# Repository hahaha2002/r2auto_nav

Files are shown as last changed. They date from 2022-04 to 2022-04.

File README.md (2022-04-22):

# r2auto_nav
Tánkyu 2310i <br/>
Group 2, Studio 2 <br/>
Ang Kai Jun, David Chong Joon Wei, Ha Zhe Li, Rayner Lim Fang Yuh, Wang Yanxiao Austin <br/>

EG2310 - Fundamentals of Systems Design, AY 21/22, <br/>
Innoovation and Design Programme, National University of Singapore (NUS). <br/>
Screen_Shot_2022-04-22_at_00 24 10_AM-removebg-preview

## Description
The Tánkyu 2310i, developed by NUS IDP students from EG2310, is a modified Robotis Co. Turtlebot 3. It is augmented with LIDAR, NFC-detection, IR-detection and a flywheel firing system to accomplish its set objectives - Autonomous navigation within a closed and connected maze, locating a loading bay demarcated by NFC tags, and firing a ping-pong ball at a target with high IR-signature.

In this repository, we are using Ubuntu 20.04.4, ROS2 Foxy and Python3.6 to explore a closed and connected maze using a left-wall following algorithm.
You may check out our project report under the [Documentations](https://github.com/hahaha2002/r2auto_nav/tree/main/Documentations) folder for more details on our robot and its mission.

## File Organisation
- [Documentations](https://github.com/hahaha2002/r2auto_nav/tree/main/Documentations) folder contain all the documentation of the Tánkyu 2310i, this includes the project report, assembly manual, full software setup guide and end user documentation.
- [navigation.py](https://github.com/hahaha2002/r2auto_nav/blob/main/navigation.py) code contains the main system and wall-following logic. This code also communicates with the mission code to allow the Tánkyu 2310i to engage on the ir signature when the conditions are met.
- [mission.py](https://github.com/hahaha2002/r2auto_nav/blob/main/mission.py) code initiates all the i2c connections and contain the firing algorithm. This code performs all necessary logic processing with the input from the NFC and IR detection systems and communicates the information to the navigation code to allow the Tánkyu 2310i to engage on the ir signature when the conditions are met.
- [Ubuntu_Files](https://github.com/hahaha2002/r2auto_nav/tree/main/Ubuntu_Files) folder is an archive of the miscellaneous code that was tested but not implemented into the final system. The code are functional independently but requires some edits to integrate it into the final system.
- [RPi_Files](https://github.com/hahaha2002/r2auto_nav/tree/main/RPi_Files) folder contains the [factory acceptance test codes](https://github.com/hahaha2002/r2auto_nav/tree/main/RPi_Files/fac_test), all required packages and other test codes for each individual subsystem. 
- [Original_Files](https://github.com/hahaha2002/r2auto_nav/tree/main/Original_Files) folder is an archive of the forked repository from [shihchengyen's r2auto_nav_repository](https://github.com/shihchengyen/r2auto_nav) and is not necessary for the Tankyu 2310i's operations.

## Calibration and configuration
### Navigation Code
Under 'Adjustable variables to calibrate wall follower', you may experiment with different parameters to calibrate the navigation algorithm to suit your needs.
| Variable name| Description| Recommended value  |
| --- |:---| ---:|
| d | Distance from wall| 0.35 |
| fd| Front distance when approaching a merging wall| d + 0.1|
| reverse_d | Distance to reverse when too close to front wall| 0.20|
| speedchange | Linear speed | 0.17|
| turning_speed_wf_fast| Fast rotate speed, used when avoiding obstacle in front| 0.75|
| turning_speed_wf_slow| Slow rotate speed, used when reversing, finding wall or too close to wall| 0.40|
| snaking_radius | Distance from wall before correcting drift | d - 0.07|
| cornering_speed_constant | Coefficient of speedchange during cornering to prevent over/under steer| 0.5|

### Mission Code
Under 'Adjustable variables to calibrate targeting' you may experiment with different parameters to calibrate the targeting algorithm to suit your needs.
| Variable name| Description| Recommended value  |
| --- |:---| ---:|
| rotatechange | Angular speed| 0.35 |
| speedchange | Linear speed | 0.20 |
| min_temp_threshold | IR live feed minimum value reference (Appears blue) | 30.0|
| max_temp_threshold | IR live feed maximum value reference (Appears red) | 35.0|
| detecting_threshold | Minimum temperature to identify target as a "Hot target" | 32.0|
| firing_threshold | Acts as a second check after centering target | 35.0|
| ir_offset | Offset angle for each IR sensor orientation (0°→0, 45°→31, 90°→69) | 31.0|

## Operating Instructions

### Installation
Tested on Ubuntu 20.04 - ROS2 Foxy <br/>
For beginners, follow our step-by-step software setup guide in our [documentations](https://github.com/hahaha2002/r2auto_nav/tree/main/Documentations) folder.<br/>
For M1 MacBook users, refer to our [video guide](https://youtu.be/suntoEurFio) for Ubuntu setup and installation. <br/>

1. Install Ubuntu 20.04 and ROS 2 Foxy using the instructions in Section 3.1 of the [Robotis e-manual](https://emanual.robotis.com/docs/en/platform/turtlebot3/quick-start/#pc-setup) (Ensure you click on the "Foxy" tab).
3. Using Ubuntu, complete the RPi in Section 3.2
4. Using Ubuntu, complete the OpenCR setup in Section 3.3 

### Set Up
1. Clone this repository onto your Ubuntu ros2 directory: <br/>
``` 
cd colcon_ws/src/auto_nav
git clone https://github.com/hahaha2002/r2auto_nav.git 
cd colcon_ws
colcon build
```
2. Copy mission.py and the RPi_files folder to the RPi: <br/>
``` 
scp -r <path to r2auto_nav directory>/mission.py ubuntu@<RPi IP address>:~/turtlebot_ws/src 
scp -r <path to r2auto_nav directory>/RPi_files ubuntu@<RPi IP address>:~/turtlebot_ws/src 
```
3. Build the package on RPi: <br/>
``` 
cd turtlebot3_ws 
colcon build 
```
4. Install the pigpio package on RPi and automate the daemon on boot:
```
sudo apt install pigpio
sudo systemctl enable pigpiod
```

### Running Instructions
1. Ssh into the RPi, `ssh ubuntu@<RPi IP Address>`
2. On the RPi, initiate the bring up `ros2 launch turtlebot3_bringup robot.launch.py'
3. On RPi, in the RPi_files directory, Start the targeting code `python3 mission.py`.
4. On Ubuntu, in the r2auto_nav directory, Start the navigation code `python3 navigation.py`.

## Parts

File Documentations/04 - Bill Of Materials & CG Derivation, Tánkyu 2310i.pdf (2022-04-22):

Bill of Materials / CG derivation,

## Tánkyu 2310i

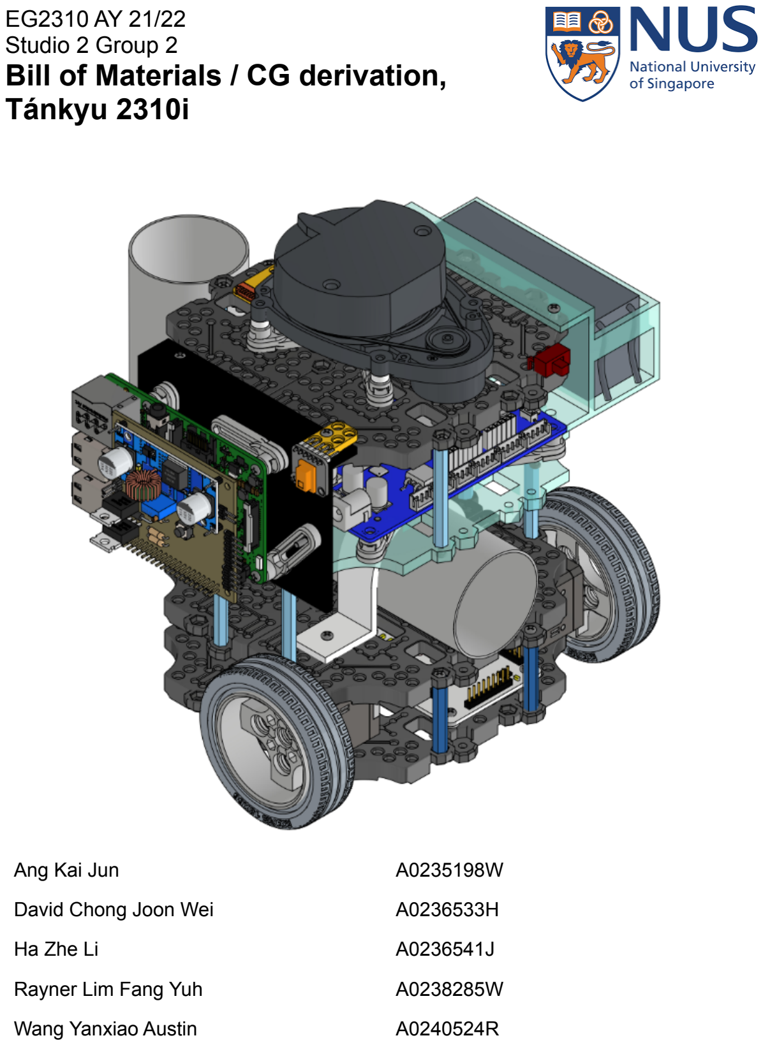
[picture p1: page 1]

EG2310 AY 21/22
Studio 2 Group 2
Ang Kai Jun | A0235198W
David Chong Joon Wei | A0236533H
Ha Zhe Li | A0236541J
Rayner Lim Fang Yuh | A0238285W
Wang Yanxiao Austin | A0240524R

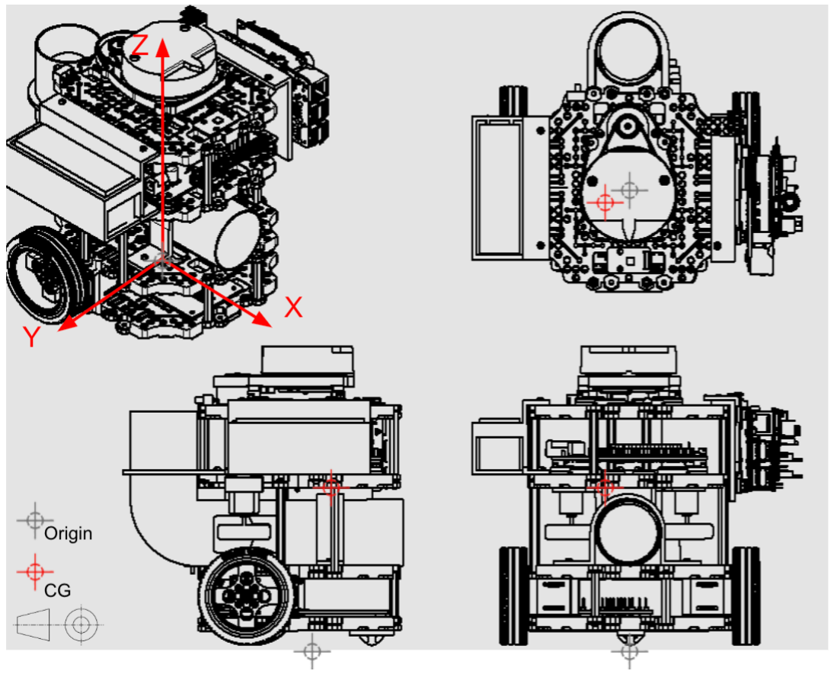
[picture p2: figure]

To find the CG, we first measure the XYZ coordinates of each component with respect to an arbitrary point on the robot. In this case we will set the reference on the ground level directly beneath the center of the waffle plate. This point will be our Origin.

Assumptions made:
1. All screws, nuts, bolts and washers’ CG are accounted for with the major component itself.
2. Parts symmetrical about the origin are assumed to have CG within the axis Z of the origin.

Table 1: Bill of Materials Calculated to 3 Decimal Places.

S/n. | Component | Weight (Kg) | Component’s CG from origin
X(m) | Y(m) | Z(m)

Level 1

1.1 | Waffle Plate lvl 1 | 0.079 | 0.000 | 0.000 | 0.015
1.2 | Ball Caster | 0.004 | -0.005 | 0.000 | 0.000
1.3 | Left Dynamixel Motor | 0.055 | 0.040 | -0.05 | 0.020
1.4 | Right Dynamixel Motor | 0.055 | 0.040 | 0.050 | 0.020
1.5 | NFC reader | 0.016 | 0.005 | 0.010 | 0.016
1.6 | Posts x4 | 0.001 | 0.000 | 0.000 | 0.035
1.7 | Left Wheel + Tire | 0.029 | 0.040 | 0.080 | 0.030
1.8 | Right Wheel + Tire | 0.029 | 0.040 | -0.080 | 0.030

Level 2

2.1 | Waffle Plate lvl 2 | 0.079 | 0.000 | 0.000 | 0.052
2.2 | Pipe clamp | 0.070 | 0.022 | 0.005 | 0.075
2.3 | Pipe | 0.120 | 0.090 | 0.005 | 0.100
2.4 | Servo mount | 0.002 | -0.037 | -0.050 | 0.063
2.5 | Servo | 0.010 | -0.035 | -0.030 | 0.065
2.6 | Posts x4 | 0.010 | 0.000 | 0.000 | 0.082

Level 3

3.1 | Acrylic Waffle Plate lvl 3 | 0.079 | 0.010 | 0.000 | 0.112
3.2 | OpenCR bracket x4 | 0.007 | 0.020 | 0.000 | 0.120
3.3 | OpenCR | 0.062 | 0.020 | 0.000 | 0.125

3.4 | Motor mount x2 | 0.020 | -0.015 | 0.000 | 0.107
3.5 | Motor + wheel x2 | 0.034 | -0.030 | 0.000 | 0.107
3.6 | Posts x4 | 0.080 | -0.028 | 0.000 | 0.140

Level 4

4.1 | Waffle Plate lvl 4 | 0.079 | 0.000 | 0.000 | 0.163
4.2 | Lidar bracket x4 | 0.007 | 0.000 | 0.000 | 0.178
4.3 | Lidar | 0.110 | -0.010 | 0.000 | 0.190
4.4 | USB2LDS | 0.002 | -0.052 | 0.000 | 0.178
4.5 | Rpi Bracket | 0.070 | 0.000 | 0.070 | 0.135
4.6 | Rpi support x4 | 0.007 | 0.015 | 0.085 | 0.127
4.7 | Rpi | 0.047 | 0.000 | 0.090 | 0.122
4.8 | PCB | 0.070 | 0.000 | 0.095 | 0.122
4.9 | IR sensor | 0.004 | 0.033 | 0.085 | 0.165
4.11 | IR bracket | 0.002 | 0.033 | 0.083 | 0.165
4.12 | Battery bracket | 0.070 | 0.000 | -0.093 | 0.145
4.13 | Battery | 0.137 | 0.000 | -0.095 | 0.137
TOTAL MASS: | | 1.384kg | - | - | -

Table 2: Moment of components Calculated to 3 Significant Figures.

Component | Xm(kgm) | Ym(kgm) | Zm(kgm)

Level 1

Waffle Plate lvl 1 | 0.000 | 0.000 | 0.00119
Ball Caster | -0.0000200 | 0.000 | 0.000
Left Dynamixel Motor | 0.00220 | -0.00275 | 0.00110
Right Dynamixel Motor | 0.00220 | 0.00275 | 0.00110
NFC reader | 0.0000800 | 0.000160 | 0.000256
Posts x4 | 0.000 | 0.000 | 0.0000350
Left Wheel + Tire | 0.00116 | 0.00232 | 0.000870
Right Wheel + Tire | 0.00116 | -0.00232 | 0.000870

Level 2

Waffle Plate lvl 2 | 0.000 | 0.000 | 0.00410
Pipe clamp | 0.00154 | 0.000350 | 0.00525
Pipe | 0.0108 | 0.000600 | 0.0120
Servo mount | 0.0000740 | 0.0001000 | 0.000126
Servo | -0.00035 | -0.000300 | 0.000650
Posts x4 | 0.000 | 0.000 | 0.00082

Level 3

Acrylic Waffle Plate lvl 3 | 0.000790 | 0.000 | 0.00885
OpenCR bracket x4 | 0.000140 | 0.000 | 0.000840
OpenCR | 0.00124 | 0.000 | 0.00775
Motor mount x2 | 0.000300 | 0.000 | 0.00214

Motor + wheel x2 | -0.00102 | 0.000 | 0.00364
Posts x4 | -0.00224 | 0.000 | 0.0112

Level 4

Waffle Plate lvl 4 | 0.000 | 0.000 | 0.0129
Lidar bracket x4 | 0.000 | 0.000 | 0.00125
Lidar | -0.00110 | 0.000 | 0.0209
USB2LDS | -0.000104 | 0.000 | 0.000356
Rpi Bracket | 0.000 | 0.00490 | 0.00945
Rpi support | 0.000420 | 0.00238 | 0.00356
Rpi | 0.00 | 0.00423 | 0.00573
PCB | 0.00 | 0.00665 | 0.00854
IR sensor | 0.000132 | 0.000340 | 0.000660
IR bracket | 0.0000660 | 0.000166 | 0.000330
Battery bracket | 0.000 | 0.00651 | 0.0102
Battery | 0.000 | 0.0130 | 0.0188
TOTAL: | 0.0175 | 0.0391 | 0.155

The overall CG position can therefore be calculated by summing the individual component moments in each axis and dividing that sum by the sum of mass of all the components.

Sum Xm(kgm) | Sum Ym(kgm) | Sum Zm(kgm)
0.0175 | 0.0391 | 0.155
Total mass = 1.384kg

CG coordinates:

X-distance(m) | Y distance(m) | Z distance (m)
0.0126 | 0.0283 | 0.112

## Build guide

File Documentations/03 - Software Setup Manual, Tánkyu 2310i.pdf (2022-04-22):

## Tánkyu 2310i, Software Setup Manual

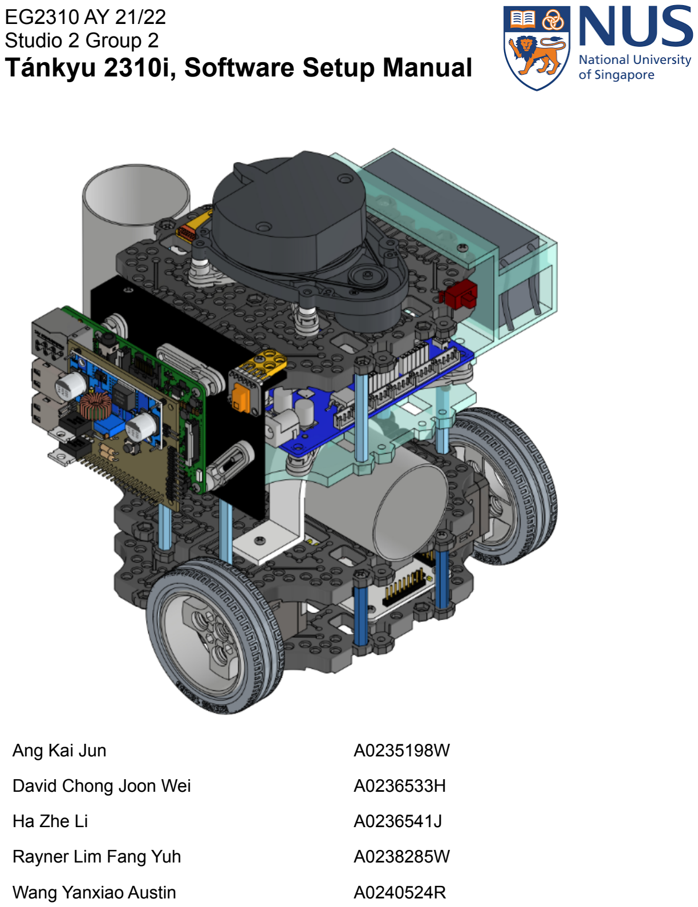
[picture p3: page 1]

EG2310 AY 21/22
Studio 2 Group 2
Ang Kai Jun | A0235198W
David Chong Joon Wei | A0236533H
Ha Zhe Li | A0236541J
Rayner Lim Fang Yuh | A0238285W
Wang Yanxiao Austin | A0240524R

## Contents Page

Contents Page | 1
1.0 Description | 2
2.0 Setup Guide | 2
2.1 On your Linux Laptop | 2
2.2 On your Raspberry Pi | 4
2.3 Optional Setup | 5
2.3.1 Keeping track of RPI IP address | 5
2.3.2 Bypassing RPi password requirement | 9
3.0 Operating Instructions: | 13
3.1 Factory Acceptance Test / Pre-mission Checks | 14
3.2 Calibration Instructions | 15
3.2.1 Navigation Code | 15
3.2.2 Mission Code | 16
4.0 References | 16

## 1.0 Description

The Tánkyu 2310i, developed by NUS IDP students from EG2310, is a modified Robotis Co. Turtlebot 3. It is augmented with LIDAR, NFC-detection, IR-detection and a flywheel firing system to accomplish its set objectives - Autonomous navigation within a closed and connected maze, locating a loading bay demarcated by NFC tags, and firing a ping-pong ball at a target with high IR-signature.

This Software Setup Manual contains detailed information on the laptop and RPi setup process. It aims to be a step-by-step guide on how to set up and operate the Tánkyu 2310i from scratch for beginners and thus contains overlapping information from our GitHub repository. For experienced users, refer to our GitHub repository for just the required packages and code.

In this guide, we will be using Ubuntu 20.04.4, ROS2 Foxy and Python3.6. This guide is correct as of 22/04/2022.

## 2.0 Setup Guide

The following will be one time setup instructions if it is your first time operating the Tankyu 2310i. Otherwise, navigate directly to Section 3.0: Operating Instructions.

## 2.1 On your Linux Laptop

1. Install Ubuntu 20.04 and ROS 2 Foxy using the instructions in Section 3.1 of the following webpage (make sure you click on the “Foxy” tab at the top of the webpage):
https://emanual.robotis.com/docs/en/platform/turtlebot3/quick-start/#pc-setup
2. Add the following to the .bashrc on your laptop:
$ export TURTLEBOT3_MODEL=burger
$ alias rteleop ='ros2 run turtlebot3_teleop teleop_keyboard'
$ alias rslam='ros2 launch turtlebot3_cartographer cartographer.launch.py'
3. Reload the .bashrc:
$ source ~/.bashrc
4. We will first create a ROS2 package $ cd ~/colcon_ws/src

$ ros2 pkg create --build-type ament_python auto_nav $ cd auto_nav/auto_nav

5. Move the file in the directory temporarily to the parent directory:
$ mv __init__.py ..
6. We are now ready to clone the GitHub repository.
(NOTE: If you would like to edit the code based on your application, you may first fork the repository on Github. After that, you may clone your Github repository by replacing the user id ‘hahaha2002’ in the code below with your user id.)
$ git clone git@github.com:hahaha2002/r2auto_nav.git
7. Move the file init.py back
$ mv ../__init__.py
8. (Optional) If you wish to commit your changes to the GitHub repository, eg. you forked the repository, configure your git environment.
$ git config --global user.email "<your email>"
$ git config --global user.name "<your user name>" $ git config --global push.default simple
9. Next, build the auto_nav package $ cd ~/colcon_ws
$ colcon build --packages-select auto_nav

10.Install the scipy Python package
$ pip3 install scipy --user
11. Install numpy and matplotlib packages $ pip3 install numpy matplotlib

## 2.2 On your Raspberry Pi

1. Using Ubuntu, burn the ROS2 Foxy image to the SD card of the R-Pi’s using the instructions starting from Section 3.2.3 at (make sure you click on the “Foxy” tab at the top of the webpage): https://emanual.robotis.com/docs/en/platform/turtlebot3/sbc_setup/#sbc-set up (https://emanual.robotis.com/docs/en/platform/turtlebot3/sbc_setup/#sbc-setup)
2. Complete the OpenCR setup in Section 3.3 https://emanual.robotis.com/docs/en/platform/turtlebot3/opencr_setup/#ope ncr-setup (https://emanual.robotis.com/docs/en/platform/turtlebot3/opencr_setup/#opencr-setup)
3. Add the following to the .bashrc on both R-Pi’s:
$ export TURTLEBOT3_MODEL=burger
$ alias rosbu='ros2 launch turtlebot3_bringup robot.launch.py'
4. Reload the .bashrc:
$ source ~/.bashrc
5. Install gpio packages
$ sudo apt-get install rpi.gpio
6. Install i2c-tools
$ sudo apt install -y i2c-tools python3-pip
7. Change permissions of /dev/i2c-1 $ sudo chmod a+rw /dev/i2c-1
8. Install i2c-tools
$ pip3 install smbus2
9. Install spidev module
$ pip3 install spidev

10.Create a ROS2 package
$ cd ~/turtlebot_ws/src
$ ros2 pkg create --build-type ament_python auto_nav $ cd auto_nav/auto_nav

11. Copy mission.py and the RPi_files folder from your laptop to the RPi (** Code run on laptop with the cloned Github repository)
$ scp <path to r2auto_nav directory>/mission.py ubuntu@<RPi IP address>:~/turtlebot_ws/src/auto_nav/auto_nav
$ scp -r <path to r2auto_nav directory>/RPi_files ubuntu@<RPi IP address>:~/turtlebot_ws/src/auto_nav/auto_nav

12.Build the auto_nav package $ cd ~/turtlebot_ws
$ colcon build --packages-select auto_nav

## 2.3 Optional Setup

This section includes optional setups to make it easier to work on the Tankyu 2310i for multiple runs.

2.3.1 Keeping track of RPI IP address
You can use a virtual machine on Amazon Web Services (AWS) to keep track of the dynamic IP address assigned to the Raspberry Pi (R-Pi) on your TurtleBot. You may do the following in Linux.
a. Sign up for a free-tier AWS account at (click the Create a new AWS account button):
https://console.aws.amazon.com/console/home?nc2=h_ct&src=header-signin (https://console.aws.amazon.com/console/home?nc2=h_ct&src=header-signin)
b. When asked to choose the Account type, select “Personal”.
c. Select “Singapore” as the Country/Region.
d. Enter a credit/debit card in order to create the account. If you follow the instructions, you will not incur any charges.
e. Enter your mobile number in order to get an access code.
f. Select the “Basic Plan” when asked to select a Support Plan.
g. Click the “Sign in to the Console” button to sign into your AWS account.

h. Click “EC2” under “AWS services”.
i. Click the “Launch Instance” button.
j. Make sure the “64-bit (x86)” option under “Amazon Linux 2 AMI (HVM), SSD Volume Type” is selected, and then click the “Select” button.
k. Make sure the “t2.micro” instance type is selected, and then click the “Review and Launch” button. The free-tier account allows you to have a t2.micro EC2 instance running 24 hours a day without any charges.
l. Click the “Launch” button.
m. When the key pair window comes up, select the “Create a new key pair” under the first drop-down menu.
n. Enter a name for your key pair (e.g. MyKeyPair), and then click the “Download Key Pair” button. A .pem file will be downloaded, which you can use to access your AWS account in the future.
o. Click the “Launch Instances” button.
p. While waiting for the instance to launch, you can click the “Services” button in the top-left of the window and select “EC2”. This will take you to the EC2 Dashboard.
q. Click on the “Instances (running)” button, which will show you information about your running instances. There should only be one entry at this point, so you can click on the instance under the “Instance ID” column. This should show you information about your instance, including the public IPv4 address. Note down the address as you will be using it for the rest of the semester.
r. You will need to change the permission settings on the key pair file, so first open up the Terminal application and check your file permissions:

ls -l ~/Downloads/MyKeyPair.pem

This should return the following:

-rw-r--r--@ | 1 | syen | staff | 1700 | Dec | 13 | 22:18
/Users/syen/Downloads/MyKeyPair.pem

indicating that the owner (i.e. you) has read and write permissions and other users only have read permissions. AWS will reject these permissions as not being secure enough, so you will need to change the permissions by doing:

chmod 400 ~/Downloads/MyKeyPair.pem

If you check your permissions again:

ls -l ~/Downloads/MyKeyPair.pem

you should see:

-r--------@ | 1 | syen | staff | 1700 | Dec | 13 | 22:18
/Users/syen/Downloads/MyKeyPair.pem

which means that only you have read permissions, and even the write permissions have been removed so you will not accidentally modify the file.

s. Now you can try accessing your EC2 instance (replace IP-address below with the IP address of your EC2 instance):

ssh -i ~/Downloads/MyKeyPair.pem ec2-user@IP-address

You might get a warning that says:

The authenticity of host '52.221.221.183 (52.221.221.183)' can't be established.
ECDSA | key | fingerprint | is
SHA256:XRs+sZbEFRleJY8H41EH4nxRG1BYj4XO5+tKWCREzlk.
Are you sure you want to continue connecting (yes/no/[fingerprint])?

You should enter “yes”. This should show you the following login screen:

__| __|_ )

_| ( / Amazon Linux 2 AMI
___|\___|___|

https://aws.amazon.com/amazon-linux-2/
7 package(s) needed for security, out of 19 available
Run "sudo yum update" to apply all updates.
[ec2-user@ip-172-31-33-20 ~]$

This means that you have successfully accessed your EC2 instance. You can type “exit” to logout.

t. In order to simplify the login process, create a SSH public-private key pair on your laptop by doing the following in your Terminal window:

ssh-keygen

Hit Return three times to use the default file name, and to accept a blank password. This will create two files in the .ssh directory in your home directory: id_rsa and id_rsa.pub

u. You can now use the following command to copy the second file to your EC2 instance (you can hit the up arrow to access your command history, and then use the left and right button to edit the command):
scp | -i | ~/Downloads/MyKeyPair.pem | ~/.ssh/id_rsa.pub
ec2-user@IP-address:~/
v. Login again to your EC2 instance (using the up arrow):

ssh -i ~/Downloads/MyKeyPair.pem ec2-user@IP-address

w. Run the ssh-keygen command to create keys on your EC2 instance:

ssh-keygen

x. Move the id_rsa.pub file from your laptop to the .ssh directory:

mv id_rsa.pub ~/.ssh/authorized_keys

y. Logout again by entering “exit”.

z. You should now be able to login without using the .pem file (use the up arrow to edit a previous command):

ssh ec2-user@IP-address

You can logout after verifying that you can login successfully.

aa.You can create an alias on your laptop using the nano editor to make logging in even easier:

nano ~/.ssh/config

bb.Enter the following (replace IP-address below with the IP address of your EC2 instance):

Host aws
HostName IP-address
User ec2-user

cc. Type Ctrl-x to exit the editor, type “y” to save the document, and hit Return to use the current file name.

dd.You should now be able to login by doing:

ssh aws

ee.Be sure that you do not shut down or restart your AWS instance as it will change the IP address of the AWS instance, and you will then need to update the address in your scripts.

2.3.2 Bypassing RPi password requirement
You can now optimise your setup so you will find it easier to work with the TurtleBot. First, we will remove the need to plug a monitor into your R-Pi in order to find out its IP address. We will do this by creating a script that will be run during startup to send the R-Pi’s IP address to your AWS instance.
a. Open a terminal window on your laptop and ssh to your R-Pi. We will then create a SSH public-private key pair on the R-Pi that will allow it to ssh to AWS to update the IP address:

ssh-keygen

Hit Return three times to use the default file name, and to accept a blank password. This will create two files in the .ssh directory in the home directory: id_rsa and id_rsa.pub

b. Display the public key on the R-Pi:

cat ~/.ssh/id_rsa.pub

c. In another Terminal window on your laptop, login to your group’s AWS account:

ssh aws

d. Edit the authorized_keys file using the nano editor:

nano ~/.ssh/authorized_keys

and paste the public key from the R-Pi into the file.

e. Exit and save the file.
f. On the R-Pi, use the nano text editor to create a file with information to connect to your AWS instance:

nano ~/.ssh/config

g. Enter the following into the file (replace IP-address below with the IP address of your EC2 instance):

host aws
HostName <IP-address>
User ec2-user
h. Exit and save the file.
i. You should now be able to do the following from your R-Pi to login to your AWS instance:

ssh aws

j. We now need to create a system service that will run whenever the R-Pi starts up:

sudo nano /etc/systemd/system/ip2aws.service

k. Enter the following into the file, which will run the ip2aws.bash script in the home directory when the R-Pi boots up:

[Unit]
After=network.service

[Service]
ExecStart=/home/ubuntu/ip2aws.bash

[Install]
WantedBy=default.target
l. We will now create the script that the service will run:

nano ~/ip2aws.bash

m. Enter the following into the file for the R-Pi, which will get the IP address, remove the space character at the end, and use the ubuntu account to save the IP address on AWS in a file named “rpi.txt”:

#!/bin/bash

myIP=`hostname -I | tr -d " "`
echo $myIP | runuser -l ubuntu -c 'ssh aws "cat - > rpi.txt"'
n. Change the permissions of the files:

chmod 744 ~/ip2aws.bash
sudo chmod 664 /etc/systemd/system/ip2aws.service
o. Register the service:

sudo systemctl daemon-reload sudo systemctl enable ip2aws.service

p. Reboot the R-Pi’s:

sudo reboot

q. Once the R-Pi’s have booted up, you should be able to check that the IP addresses are correctly saved into the rpi.txt file by doing the following from your laptop:

ssh aws cat rpi.txt

r. Edit the .bashrc file on your laptop to add the following at the end:

alias sshrp='ssh ubuntu@`ssh aws cat rpi.txt`'

alias sshrp2='ssh ubuntu@`ssh aws cat rpi2.txt`'

s. Reload the bashrc file:

$ source ~/.bashrc

t. Copy the ssh public key from your laptop to the R-Pi’s:

ssh-copy-id ubuntu@`ssh aws cat rpi.txt`

u. You should now be able to ssh to the TurtleBot R-Pi by doing:

$ sshrp

# 3.0Operating Instructions:

1. Turn on the Tánkyu 2310i
2. SSH into the RPi on the turtlebot.
$ sshrp

Refer to section 2.3 if you have not set up an alias for sshrp. Alternatively, you may manually ssh into your RPI by using
$ ssh ubuntu@<RPI IP address>
3. Run the bring up on the RPi
$ rosbu
4. Start the mission.py code on the RPi
$ python3 mission.py
5. The mission.py file should automatically run the pigpio daemon, if you encounter an error with the pigpio daemon not running automatically, enter this command and repeat step 4.
$ sudo pigpiod
6. Start the navigation.py code from your linux system
$ python3 navigation.py
7. The navigation.py code should open a RViz window automatically, if you encounter an error with the RViz window not opening automatically, you can manually open a RViz window by entering this command (refer to section 2.3 if you have not set up an alias for RViz).
$ rslam
8. To terminate the program, press ‘ctrl + C’.
9. You should see three new files in the directory:
a. mazemapfinally.png
b. lidar.txt
c. map.txt

## 3.1 Factory Acceptance Test / Pre-mission Checks

The Factory Acceptance Test or Pre-mission Checks aim to ensure each individual system of the Tánkyu 2310i is operational before the mission. It also acts as a way to isolate faults or for modular testing if the need arises. It is recommended that the Factory Acceptance Tests be run before every mission to ensure a successful mission.

1. Turn on the Tánkyu 2310i.
2. SSH into the RPi on the turtlebot.
$ sshrp
3. Navigate to the fac_test directory.
$ cd RPi_Files/fac_test
4. Run the code for each individual system to test.
$ python3 <code name>
code name | How to trigger the test | Expected outcome | Remarks
servo_test | Enter an integer from 0 to 180 | Servo moves to specified angle | Ensure no obstructions before actuating servo, else the servo may fry.
motor_test | Enter either 0 or 1. 0: Stop motor 1: Start motor | Both motors run on command. Left motor spins anti-clockwise Right motor spins clockwise | Ensure no obstructions between motors before running code. Motors do not have enough torque to eject a wedged ping-pong ball.
nfc_test | Place an nfc tag below PN532 | Terminal reads “NFC Detected”. | To check i2c connectivity, use

$ sudo i2cdetect -y 1

ir_publisher | Nil | Terminal starts publishing messages to ir_data topic

To check i2c
connectivity, use
$ sudo i2cdetect -y 1
ir_test | Place a hot object in front of the AMG8833 | Live feed of the temperature array appears. Terminal reads out the hottest temperature.

Run this code on
laptop after running
ir_publisher on RPi

## 3.2 Calibration Instructions

3.2.1 Navigation Code
Under 'Adjustable variables to calibrate wall follower', you may experiment with different parameters to calibrate the navigation algorithm to suit your needs.
Variable name | Description | Recommended value
d | Distance from wall | 0.35
fd | Front distance when approaching a merging wall | d + 0.1
reverse_d | Distance to reverse when too close to front wall | 0.20
speedchange | Linear speed | 0.17
turning_speed_wf _fast | Fast rotate speed, used when avoiding obstacle in front | 0.75
turning_speed_wf _slow | Slow rotate speed, used when reversing, finding wall or too close to wall | 0.40
snaking_radius | Distance from wall before correcting drift | d - 0.07
cornering_speed_ constant | Coefficient of speedchange during cornering to prevent over/under steer | 0.5

3.2.2 Mission Code
Under 'Adjustable variables to calibrate targeting' you may experiment with different parameters to calibrate the targeting algorithm to suit your needs.
Variable name | Description | Recommended value
rotatechange | Angular speed | 0.35
speedchange | Linear speed | 0.20
min_temp_thresh old | IR live feed minimum value reference (Appears blue) | 30.0
max_temp_thresh old | IR live feed maximum value reference (Appears red) | 35.0
detecting_thresho ld | Minimum temperature to identify target as a "Hot target" | 32.0
firing_threshold | Acts as a second check after centering target | 35.0
ir_offset | Offset angle for each IR sensor orientation (0°→0, 45°→31, 90°→69) | 31.0

## 4.0 References

Part of the Software Setup Manual were adapted from the lab handouts produced by Prof Yen Shih Cheng, Director of NUS, Innovation and Design Programme, as part of the EG2310 - Fundamentals of Systems Design module.

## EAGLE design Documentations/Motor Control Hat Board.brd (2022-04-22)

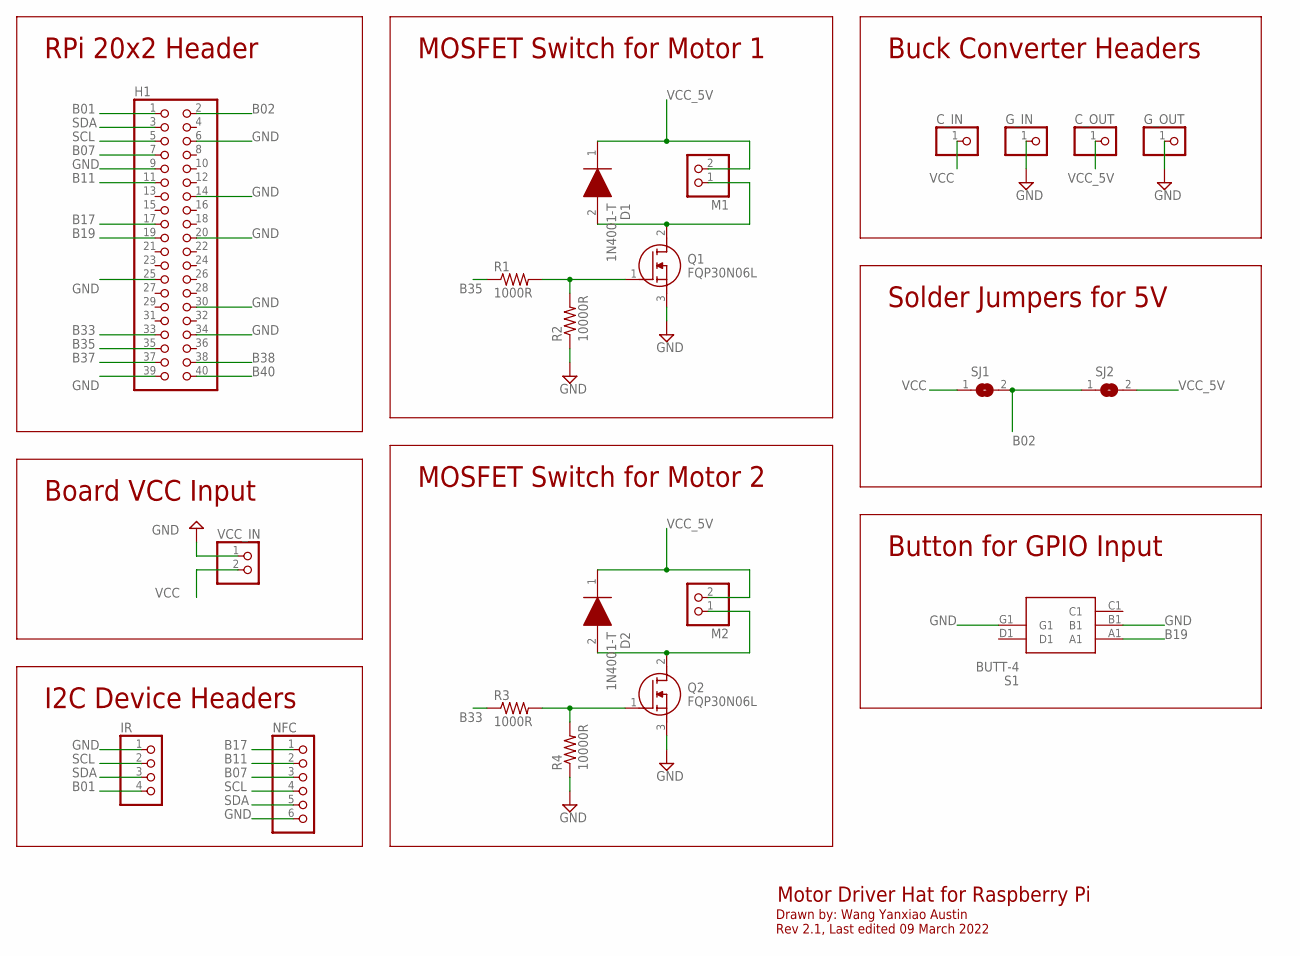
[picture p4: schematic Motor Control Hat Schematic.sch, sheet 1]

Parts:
C_IN: PINHD-1X1; 1X01
C_OUT: PINHD-1X1; 1X01
D1, D2: 1N4001-T; DIOAD1408W86L464D236
G_IN: PINHD-1X1; 1X01
G_OUT: PINHD-1X1; 1X01
H1: PINHD-2X20; 2X20
IR: PINHD-1X4; 1X04
M1, M2: PINHD-1X2; 1X02
NFC: PINHD-1X6; 1X06
Q1, Q2: FQP30N06L; TO254P470X1016X2019-3P
R1, R3: 1000R; 0207/10
R2, R4: 10000R; 0207/10
S1: BUTT-4; BUTT4
SJ1, SJ2: SJ
VCC_IN: PINHD-1X2; 1X02

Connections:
B01: H1.1, IR.4
B02: H1.2, SJ1.2, SJ2.1
B07: H1.7, NFC.3
B11: H1.11, NFC.2
B17: H1.17, NFC.1
B19: H1.19, S1.A1
B33: H1.33, R3.1
B35: H1.35, R1.1
B37: H1.37
B38: H1.38
B40: H1.40
GND: G_IN.1, G_OUT.1, H1.6, H1.9, H1.14, H1.20, H1.25, H1.30, H1.34, H1.39, IR.1, NFC.6, Q1.3 (S), Q2.3 (S), R2.1, R4.1, S1.B1, S1.G1, VCC_IN.1
unnamed: Q1.1 (G), R1.2, R2.2
unnamed: D1.2 (A), M1.1, Q1.2 (D)
unnamed: Q2.1 (G), R3.2, R4.2
unnamed: D2.2 (A), M2.1, Q2.2 (D)
SCL: H1.5, IR.2, NFC.4
SDA: H1.3, IR.3, NFC.5
VCC: C_IN.1, SJ1.1, VCC_IN.2
VCC_5V: C_OUT.1, D1.1 (K), D2.1 (K), M1.2, M2.2, SJ2.2

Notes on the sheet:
Motor Driver Hat for Raspberry Pi
Drawn by: Wang Yanxiao Austin Rev 2.1, Last edited 09 March 2022
RPi 20x2 Header
Board VCC Input
MOSFET Switch for Motor 1
MOSFET Switch for Motor 2
I2C Device Headers
Buck Converter Headers
Solder Jumpers for 5V
Button for GPIO Input

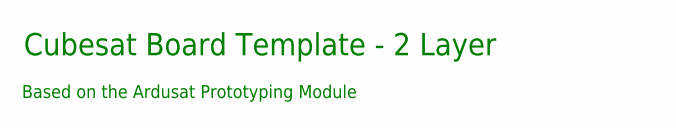
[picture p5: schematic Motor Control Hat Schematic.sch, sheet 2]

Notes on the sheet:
Cubesat Board Template - 2 Layer
Based on the Ardusat Prototyping Module

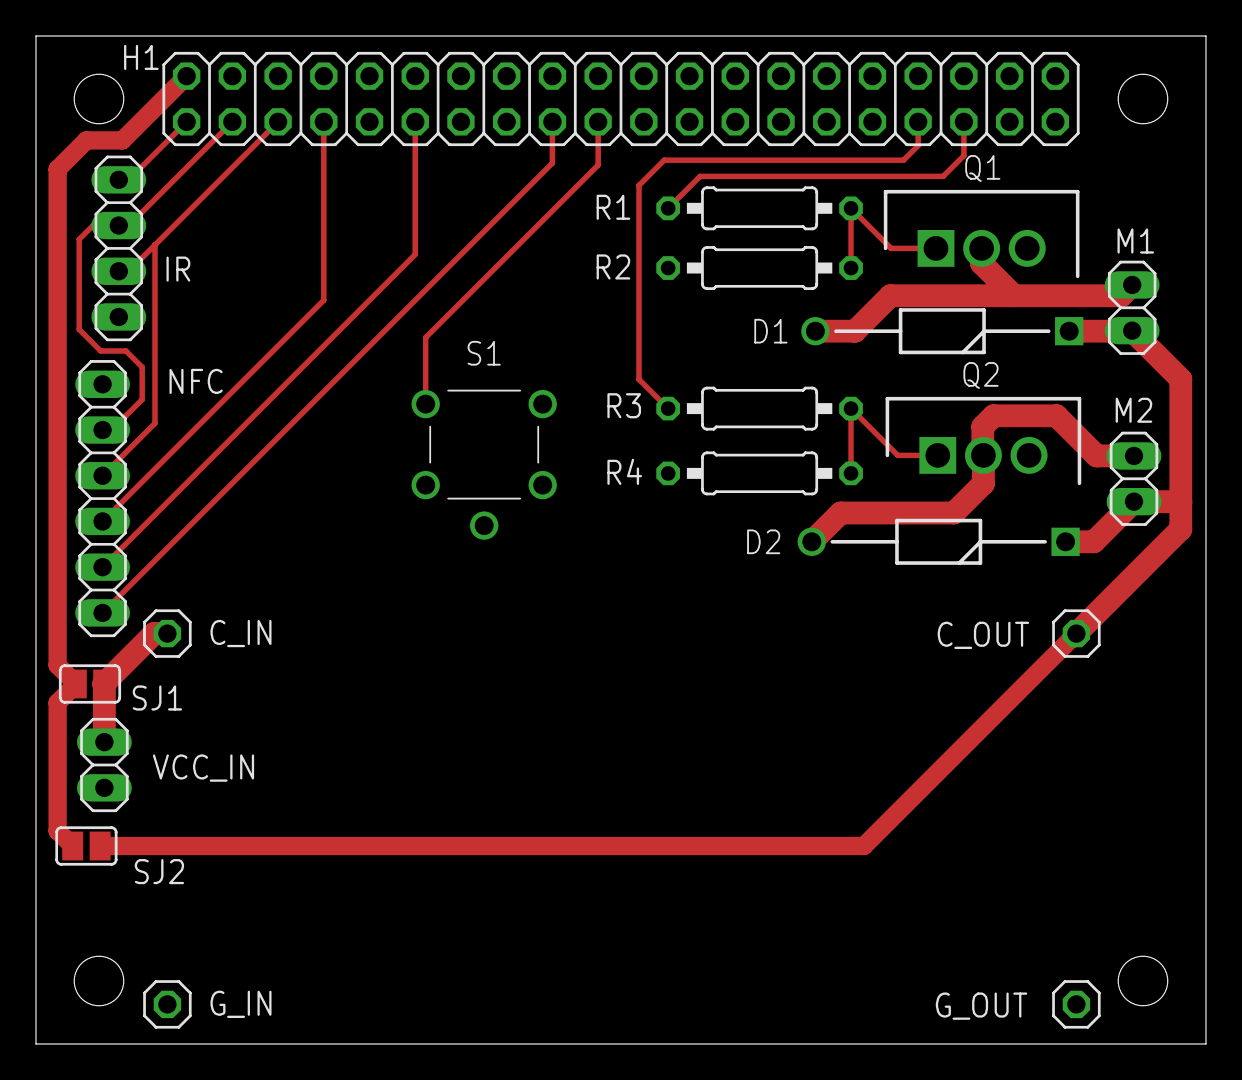
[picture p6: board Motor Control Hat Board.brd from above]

Board: 2 copper layers, 65.0 x 56.0 mm, 21 parts (0 on the bottom side), 17 nets.

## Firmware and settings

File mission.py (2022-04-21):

import time

## import thermal sensor requirements
import busio
import board
import adafruit_amg88xx

## import motor requirements
import RPi.GPIO as GPIO

## import NFC requirements
from pn532 import *

## import servo requirements
import pigpio

## import ros requirements
import numpy as np
import rclpy
from rclpy.node import Node
from std_msgs.msg import String
from geometry_msgs.msg import Twist, Pose
from rclpy.qos import qos_profile_sensor_data
from sensor_msgs.msg import LaserScan
from nav_msgs.msg import Odometry
import math
import cmath

## constants
isDoneLoading = False
isDoneShooting = False
rotatechange = 0.5
speedchange = 0.2
min_temp_threshold = 30.0
max_temp_threshold = 35.0
detecting_threshold = 32.0
firing_threshold = 35.0

# offset angle for ir (0:0 / 45:31 / 90:69)
ir_offset = 31

## messages sent
NFC_found_msg = 'LOADING ZONE'
load_finish_msg = 'FINISH LOADING'
target_status = 'Not detected'
target_detected_msg = 'Detected'
finish_shooting_msg = "FINISHED SHOOTING"

## INITIALISE IR SENSOR
try:
    i2c = busio.I2C(board.SCL, board.SDA)
    amg = adafruit_amg88xx.AMG88XX(i2c)
except:
    print('Please check wiring of IR sensor')

## INITIALISE NFC SENSOR
try:
    pn532 = PN532_I2C(debug=False, reset=4, req=17)
    pn532.SAM_configuration()
except:
    print('Please check wiring of NFC sensor')

## Set up Thermal Camera
i2c = busio.I2C(board.SCL, board.SDA)
amg = adafruit_amg88xx.AMG88XX(i2c)

## Set up servo
servo_pin = 14
servo = pigpio.pi()
servo.set_mode(servo_pin, pigpio.OUTPUT)
servo.set_PWM_frequency(servo_pin,50)
servo.set_servo_pulsewidth(servo_pin, 500)

## Set up motor
GPIO.setmode(GPIO.BCM)
GPIO.setwarnings(False) # Ignore warning for now
motor_pin1 = 13
motor_pin2 = 19
GPIO.setup(motor_pin1, GPIO.OUT)
GPIO.setup(motor_pin2, GPIO.OUT)

## Set up button
button_pin_out = 23
button_pin_in = 24
GPIO.setup(button_pin_out, GPIO.OUT)
GPIO.setup(button_pin_in, GPIO.IN, pull_up_down=GPIO.PUD_DOWN)
# Set pin 10 to be an input pin and set initial value to be pulled low (off)



class mission(Node):
    def __init__(self):
        super().__init__('mission')

        ## NFC publisher
        self.NFC_publisher_ = self.create_publisher(String, 'NFC', 10)
        timer_period = 0.5
        self.NFC_publish = self.create_timer(timer_period, self.send_nfc_status)

        ## Velocity publisher
        self.vel_publisher = self.create_publisher(Twist, 'cmd_vel', 10)

        ## Firing publisher
        self.firing_publisher = self.create_publisher(
            String, 'targeting_status', 10)
        timer_period = 0.5  # seconds
        self.firing_publish = self.create_timer(timer_period, self.send_firing_status)

        ## Lidar subscriber
        self.lidar_subscription = self.create_subscription(
            LaserScan,
            'scan',
            self.lidar_callback,
            qos_profile_sensor_data)
        self.lidar_subscription  # prevent unused variable warning

        ## Odom subscriber
        self.odom_subscription = self.create_subscription(
            Odometry,
            'odom',
            self.odom_callback,
            10)
        self.odom_subscription #prevent unused variable warning
        '''
        ## Position from map subscriber
        self.pos_subscription = self.create_subscription(Pose, '/map2base', self.pos_callback, 10)
        self.pos_subscription  # prevent unused variable warning
        # initialize variables
        '''
        self.roll = 0.0
        self.pitch = 0.0
        self.yaw = 0.0


    ## Callback functions

    def send_nfc_status(self):
        global NFC_found_msg
        msg = String()
        if not isDoneLoading:
            msg.data = NFC_found_msg
        else:
            msg.data = load_finish_msg
        self.NFC_publisher_.publish(msg)

    def send_firing_status(self):
        global target_status
        msg = String()
        msg.data = target_status
        self.firing_publisher.publish(msg)

    def lidar_callback(self, msg):
        laser_range = np.array(msg.ranges)
        laser_front = laser_range[0:4]
        np.append(laser_front, laser_range[-1:-4:-1])
        laser_front[laser_front==0] = np.nan
        try:
            self.distance = np.nanmin(laser_front)
        except ValueError:
            self.distance = 9999


    def odom_callback(self, msg):
        # self.get_logger().info(msg)
        # self.get_logger().info('In odom_callback')
        orientation_quat =  msg.pose.pose.orientation
        self.roll, self.pitch, self.yaw = self.euler_from_quaternion(orientation_quat.x, orientation_quat.y, orientation_quat.z, orientation_quat.w)
    '''
    def pos_callback(self, msg):
        global euler_from_quaternion, orientation_quat
        orientation_quat =  msg.orientation
        self.roll, self.pitch, self.yaw = self.euler_from_quaternion(orientation_quat.x, orientation_quat.y, orientation_quat.z, orientation_quat.w)
    '''

    ################################################################
    ## Helper functions

    def stopbot(self):
        twist = Twist()
        twist.linear.x = 0.0
        twist.angular.z = 0.0
        self.vel_publisher.publish(twist)


    def move_forward(self):
        twist = Twist()
        twist.linear.x = speedchange
        twist.angular.z = 0.0
        self.vel_publisher.publish(twist)
        time.sleep(0.2)
        self.stopbot()


    def euler_from_quaternion(self, x, y, z, w):
        """
        Convert a quaternion into euler angles (roll, pitch, yaw)
        roll is rotation around x in radians (counterclockwise)
        pitch is rotation around y in radians (counterclockwise)
        yaw is rotation around z in radians (counterclockwise)
        """
        t0 = +2.0 * (w * x + y * z)
        t1 = +1.0 - 2.0 * (x * x + y * y)
        roll_x = math.atan2(t0, t1)

        t2 = +2.0 * (w * y - z * x)
        t2 = +1.0 if t2 > +1.0 else t2
        t2 = -1.0 if t2 < -1.0 else t2
        pitch_y = math.asin(t2)

        t3 = +2.0 * (w * z + x * y)
        t4 = +1.0 - 2.0 * (y * y + z * z)
        yaw_z = math.atan2(t3, t4)

        return roll_x, pitch_y, yaw_z # in radians


    def rotate(self, rot_angle):
        rclpy.spin_once(self)
        rclpy.spin_once(self)
        rclpy.spin_once(self)
        print('rotating ', rot_angle)
        # self.get_logger().info('In rotatebot')
        # create Twist object
        twist = Twist()

        # get current yaw angle
        current_yaw = self.yaw
        initial_yaw = current_yaw
        # log the info
        self.get_logger().info('Current: %f' % math.degrees(current_yaw))
        # we are going to use complex numbers to avoid problems when the angles go from
        # 360 to 0, or from -180 to 180
        c_yaw = complex(math.cos(current_yaw),math.sin(current_yaw))
        # calculate desired yaw
        target_yaw = current_yaw + math.radians(rot_angle)
        # convert to complex notation
        c_target_yaw = complex(math.cos(target_yaw),math.sin(target_yaw))
        self.get_logger().info('Desired: %f' % math.degrees(cmath.phase(c_target_yaw)))
        # divide the two complex numbers to get the change in direction
        c_change = c_target_yaw / c_yaw
        # get the sign of the imaginary component to figure out which way we have to turn
        c_change_dir = np.sign(c_change.imag)
        # set linear speed to zero so the TurtleBot rotates on the spot
        twist.linear.x = 0.0
        # set the direction to rotate
        twist.angular.z = c_change_dir * 0.5
        # start rotation
        self.vel_publisher.publish(twist)

        # we will use the c_dir_diff variable to see if we can stop rotating
        c_dir_diff = c_change_dir
        # self.get_logger().info('c_change_dir: %f c_dir_diff: %f' % (c_change_dir, c_dir_diff))
        # if the rotation direction was 1.0, then we will want to stop when the c_dir_diff
        # becomes -1.0, and vice versa
        count = 0
        while(c_change_dir * c_dir_diff > 0):
            # allow the callback functions to run
            rclpy.spin_once(self)
            current_yaw = self.yaw
            #check if new current yaw differ by initial yaw by more than around 1 degree
            # (in radians)
            if count == 0 and abs(current_yaw - initial_yaw) > 0.03:
                print('here')
                # we are going to use complex numbers to avoid problems when the angles go from
                # 360 to 0, or from -180 to 180
                c_yaw = complex(math.cos(current_yaw),math.sin(current_yaw))
                # calculate desired yaw
                target_yaw = current_yaw + math.radians(rot_angle)
                # convert to complex notation
                c_target_yaw = complex(math.cos(target_yaw),math.sin(target_yaw))
                self.get_logger().info('Desired: %f' % math.degrees(cmath.phase(c_target_yaw)))
                # divide the two complex numbers to get the change in direction
                c_change = c_target_yaw / c_yaw
                # get the sign of the imaginary component to figure out which way we have to turn
                c_change_dir = np.sign(c_change.imag)
            if count == 0:
                count += 1
                print(current_yaw - initial_yaw)
            # convert the current yaw to complex form
            c_yaw = complex(math.cos(current_yaw),math.sin(current_yaw))
            self.get_logger().info('Current Yaw: %f' % math.degrees(current_yaw))
            # get difference in angle between current and target
            c_change = c_target_yaw / c_yaw
            # get the sign to see if we can stop
            c_dir_diff = np.sign(c_change.imag)
            # self.get_logger().info('c_change_dir: %f c_dir_diff: %f' % (c_change_dir, c_dir_diff))

        #self.get_logger().info('End Yaw: %f' % math.degrees(current_yaw))
        # set the rotation speed to 0
        twist.angular.z = 0.0
        # stop the rotation
        self.vel_publisher.publish(twist)

    def move_servo(self, direction):
        global servo_pin
        duty = int((2000*direction/180)+500)
        servo.set_servo_pulsewidth(servo_pin, duty)
        time.sleep(0.1)


    ################################################################
    ## Phase 1 - Search for NFC

    def nfc_search(self):
        rclpy.spin_once(self)
        loading_bay_found = False
        print('Mission - [1] - Searching for loading bay')
        while not loading_bay_found:
            # Check if a card is available to read
            nfc_reading = pn532.read_passive_target(timeout=0.5)
            print('.', end="")
            # Try again if no card is available.
            if nfc_reading is None:
                continue
            print('Mission - [2] - Arrived at loading bay')
            loading_bay_found = True
            self.send_nfc_status()

    def search(self):
        global isDoneLoading

        # Locate loading bay to retrieve payload
        rclpy.spin_once(self)
        self.nfc_search()

        # Loading balls
        GPIO.output(button_pin_out, 1)
        while not isDoneLoading:
            if GPIO.input(button_pin_in) == GPIO.HIGH:
                isDoneLoading = True
                print('Mission - [3] - Balls loaded, resuming mission')
                GPIO.output(button_pin_out, 0)
                time.sleep(3)
        self.send_nfc_status()

    #################################################################
    ## Phase 2 - Search and destroy

    def find_target(self):
        # See if target found
        global target_status, target_detected_msg
        target_found = False

        while not target_found:
            for row in amg.pixels:
                for temp in row:
                    if temp > detecting_threshold:
                        target_found = True


        # Target found, communicate with wallfollower to stop working
        target_status = target_detected_msg
        self.send_firing_status()
        #self.get_logger().info('Publishing: "%s"' % target_status)
        self.stopbot()
        time.sleep(1)


    def centre_target(self):
        global target_found
        centered = False

        while not centered:
            screen = amg.pixels
            max_row = 0
            max_column = 0
            max_value = 0.0
            for row in range(len(screen)):
                for column in range(len(screen[row])):
                    current_value = screen[row][column]
                    if current_value > max_value:
                        max_row = row
                        max_column = column
                        max_value = current_value
            # centre max value between column 3 and 4
            if max_column < 3:
                # spin anti-clockwise
                twist = Twist()
                twist.linear.x = 0.0
                twist.angular.z = rotatechange
                self.vel_publisher.publish(twist)
            elif max_column > 4:
                # spin clockwise
                twist = Twist()
                twist.linear.x = 0.0
                twist.angular.z = rotatechange * -1
                self.vel_publisher.publish(twist)
            else:
                centered = True
                print('Mission - [5] - Target Centered')
        self.stopbot()

    def targetting(self):
        global message_sent, servo_pin, motor_pin, ir_offset
        self.rotate_angle = ir_offset
        self.d = 0.7
        print('Mission - [4] - Searching for "Hot target"...')

        # find the target
        self.find_target() #stopped here

        # centre the target
        self.centre_target()
        time.sleep(1)

        # rotate to forward facing the target
        print('Mission - [6] - Rotating')
        self.rotate(-1) # problems with first time rotating on our robot
        self.rotate(- self.rotate_angle)
        time.sleep(1)
        # move forward until close enough to target
        rclpy.spin_once(self)
        #print(self.distance)
        if self.distance > self.d:
            while self.distance > self.d:
                print(self.distance)
                rclpy.spin_once(self)
                self.move_forward()
            self.stopbot()

            # Recheck center
            print('Mission - [6] - Rotating')
            rclpy.spin_once(self)
            self.rotate(1)
            self.rotate(self.rotate_angle)
            time.sleep(1)
            rclpy.spin_once(self)
            print('Mission - [7] - Re-centering')
            self.centre_target()
            print('Mission - [6] - Rotating')
            time.sleep(1)
            rclpy.spin_once(self)
            self.rotate(-1)
            self.rotate(-self.rotate_angle)
        print('Mission - [8] - Firing')

    def fire(self):
        global target_status, finish_shooting_msg, motor_pin

        # run  motor
        print('Mission - [9a] - Spool motors')
        GPIO.output(motor_pin1, 1)
        GPIO.output(motor_pin2, 1)
        time.sleep(2)

        # open servo gate
        print('Mission - [10a] - Opening servo gate')
        self.move_servo(90)
        time.sleep(5)
        print('Mission - [10b] - Closing servo gate')
        self.move_servo(0)

        # Send message that the target has finished shooting
        #self.get_logger().info("Finished shooting")
        target_status = finish_shooting_msg
        self.send_firing_status()
        #self.get_logger().info('Publishing: "%s"' % target_status)

        # Stop the DC Motor
        GPIO.output(motor_pin1, 0)
        GPIO.output(motor_pin2, 0)
        print('Mission - [9b] - Stop motors')
        #self.get_logger().info("Stopped the DC Motor")

        # Cleanup all GPIO
        GPIO.cleanup()
        #self.get_logger().info("Cleaned up GPIO")



def main(args=None):
    rclpy.init(args=args)

    MSN = mission()
    MSN.search() #Continuously search for NFC
    MSN.targetting()
    MSN.fire()
    MSN.destroy_node() #Destroy node explicitly, optional otherwise it will be done wh>
    rclpy.shutdown()


if __name__ == '__main__':
    main()

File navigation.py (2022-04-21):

# Copyright 2016 Open Source Robotics Foundation, Inc.
#
# Licensed under the Apache License, Version 2.0 (the "License");
# you may not use this file except in compliance with the License.
# You may obtain a copy of the License at
#
#     http://www.apache.org/licenses/LICENSE-2.0
#
# Unless required by applicable law or agreed to in writing, software
# distributed under the License is distributed on an "AS IS" BASIS,
# WITHOUT WARRANTIES OR CONDITIONS OF ANY KIND, either express or implied.
# See the License for the specific language governing permissions and
# limitations under the License.

import rclpy
from rclpy.node import Node
from nav_msgs.msg import Odometry
from geometry_msgs.msg import Twist, Point, Pose
from rclpy.qos import qos_profile_sensor_data
from sensor_msgs.msg import LaserScan
from nav_msgs.msg import OccupancyGrid
from std_msgs.msg import Float64MultiArray, String
import numpy as np
import tf2_ros
from tf2_ros import LookupException, ConnectivityException, ExtrapolationException, TransformException
import cv2
import math
import cmath
import time
import matplotlib.pyplot as plt
from PIL import Image
import scipy.stats
import os

## Stores known frames and offers frame graph requests
from tf2_ros.buffer import Buffer

## Easy way to request and receive coordinate frame transform information
from tf2_ros.transform_listener import TransformListener

## Open up rviz for lidar map everytime navigation is running
os.system("gnome-terminal --command='ros2 launch turtlebot3_cartographer cartographer.launch.py'")


## Adjustable variables to calibrate wall follower
d = 0.45 #Distance from wall
fd = d + 0.1
reverse_d = 0.20 #Distance threshold to reverse
speedchange = 0.2 #Linear speed
back_angles = range(150, 210 + 1, 1)
turning_speed_wf_fast = 0.8  #Fast rotate speed
turning_speed_wf_slow = 0.45  #Slow rotate speed
snaking_radius = d - 0.07  #Amount of variation accepted from wall
cornering_speed_constant = 0.5 #percentage of speed change wwhen cornering

## Variables for map file saved at the end of the mission
scanfile = 'lidar.txt'
mapfile = 'map.txt'
myoccdata = np.array([])
occ_bins = [-1, 0, 100, 101]
map_bg_color = 1

## Boolean variables
isTargetDetected = False
isDoneShooting = False
isLoadingBayFound = False
isDoneLoading = False
isMapDone = False

## Robot state dictionary
state_ = 0
state_dict_ = {
    0: 'Find the wall',
    1: 'Turn right',
    2: 'Follow the wall',
    3: 'U- Turn',
    4: 'Initial positioning',
    5: 'Reverse',
    'A': 'NFC Found, waiting to receive paylaod',
    'B': 'Payload received, continuing wall-following',
    'C': 'Hot target detected, initiating firing sequence',
    'D': 'Target eliminated',
}

## Robot state variables
position_ = Point()
yaw_ = 0
# machine state
bug_state_ = -1
bug_state_dict_ = {
    -1: 'init',
    0: 'Turn',
    1: 'Go Straight',
    2: 'Halt',
}

## Waypoint dictionary
waypoint_dict = {
    1: 'nil'
}

## Convert a quarternion into euler angles
# code from https://automaticaddison.com/how-to-convert-a-quaternion-into-euler-angles-in-python/
def euler_from_quaternion(x, y, z, w):
    """
    Convert a quaternion into euler angles (roll, pitch, yaw)
    roll is rotation around x in radians (counterclockwise)
    pitch is rotation around y in radians (counterclockwise)
    yaw is rotation around z in radians (counterclockwise)
    """
    t0 = +2.0 * (w * x + y * z)
    t1 = +1.0 - 2.0 * (x * x + y * y)
    roll_x = math.atan2(t0, t1)
    t2 = +2.0 * (w * y - z * x)
    t2 = +1.0 if t2 > +1.0 else t2
    t2 = -1.0 if t2 < -1.0 else t2
    pitch_y = math.asin(t2)
    t3 = +2.0 * (w * z + x * y)
    t4 = +1.0 - 2.0 * (y * y + z * z)
    yaw_z = math.atan2(t3, t4)

    return roll_x, pitch_y, yaw_z  # in radians




class AutoNav(Node):

    def __init__(self):
        super().__init__('auto_nav')

        # create publisher for moving TurtleBot
        self.publisher_ = self.create_publisher(Twist, 'cmd_vel', 10)

        # create subscription to messages from the targeting node
        self.targeting_subscription = self.create_subscription(
            String,
            'targeting_status',
            self.target_callback,
            10)
        self.targeting_subscription  # prevent unused variable warning

        # create subscription to track orientation
        self.odom_subscription = self.create_subscription(
            Odometry,
            'odom',
            self.odom_callback,
            10)
        self.odom_subscription  # prevent unused variable warning
        # initialize variables
        self.roll = 0
        self.pitch = 0
        self.yaw = 0

        # create subscription to track occupancy
        self.occ_subscription = self.create_subscription(
            OccupancyGrid,
            'map',
            self.occ_callback,
            qos_profile_sensor_data)
        self.occ_subscription  # prevent unused variable warning
        self.occdata = np.array([])
        self.tfBuffer = tf2_ros.Buffer()
        self.tfListener = tf2_ros.TransformListener(self.tfBuffer, self)

        # create subscription to track lidar
        self.scan_subscription = self.create_subscription(
            LaserScan,
            'scan',
            self.scan_callback,
            qos_profile_sensor_data)
        self.scan_subscription  # prevent unused variable warning
        self.laser_range = np.array([])
        self.tfBuffer = tf2_ros.Buffer()
        self.tfListener = tf2_ros.TransformListener(self.tfBuffer, self)

        # create subscription to track NFC
        self.nfc_subscription = self.create_subscription(
            String,
            'NFC',
            self.nfc_callback,
            qos_profile_sensor_data)
        self.scan_subscription  # prevent unused variable warning

        ### Map2base requirements
        self.declare_parameter('target_frame', 'base_footprint')
        self.target_frame = self.get_parameter(
        'target_frame').get_parameter_value().string_value

        self.tf_buffer = Buffer()
        self.tf_listener = TransformListener(self.tf_buffer,self, spin_thread=True)
        self.mapbase = None
        self.map2base = self.create_publisher(Pose, '/map2base', 10)
        timer_period = 0.05
        self.timer = self.create_timer(timer_period, self.timer_callback)


    def target_callback(self, msg):
        global isTargetDetected, isDoneShooting, waypoint_dict,position
        # communicates with mission code to receive status updates
        if (msg.data == 'Detected'):
            isTargetDetected = True
            isDoneShooting = False
            ## To put temperature detected and waypoint in a dictionary
            waypoint_dict[2] = position #make RPi send temp, replace 2 with that temp
            self.change_state('C')
        elif (msg.data == 'FINISHED SHOOTING'):
            isDoneShooting = True
            isTargetDetected = False
            self.change_state('D')
        else:
            isTargetDetected = False
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

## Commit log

2022-03-18 Moved calibration variables to global variables Added smarter initial move(moves to closest wall) Implemented starting waypoint, if returns without NFC, increases distance from wall
2022-04-02 added bug0 integration, not finalised
    [navigation.py]
2022-04-05 combine bug and navi code
    [navigationcombine.py]
2022-04-07 commented out print statements
2022-04-07 change motor and servo pin
2022-04-07 switched GPIO pins
2022-04-10 calibration of parameters
2022-04-10 reverted to not publishing waypoint temp, cannot publish int
    [navigationcombine.py]
2022-04-11 Added comments and standardised print statements
2022-04-11 changed yaw subscriber
2022-04-11 reverted back to OpenCR yaw data
2022-04-12 calibrated firing rotation
2022-04-12 calibrate for final run
2022-04-20 updated GPIO pin
